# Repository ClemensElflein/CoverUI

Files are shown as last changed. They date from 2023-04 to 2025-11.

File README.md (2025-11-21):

# CoverUI for [OpenMower](https://github.com/ClemensElflein/OpenMower)

 

## About

This repository contains the firmware files required to use the mowers CoverUI (ButtonBoard).

## Variants

1. Custom DIY CoverUI-PCB which replaces the stock (top-cover) PCB.<br>
 Please check the [Cover UI board assembly instructions](<https://openmower.de/docs/cover-ui-assembly/>) for more detailed infos.<br>
 Also available in [Vermut's Shop](https://shop.devops.care/10-openmower) (as part of his 'Upgrade Kit')
1. Stock YardForce CoverUI for the following models:
   1. Classic 500 (STM32 & GD32 MCU)
   2. Classic 500B (STM32 & GD32 MCU)
   3. SA/SC/NX-Type (10 Buttons, 12 LEDs), PCB labeled with RM-ECOW-V1.0.0 (STM32 MCU)
   4. SA/SC/NX-Type (9 Buttons, 11 LEDs), PCB labeled with RM-ECOW-V1.1.0 (STM32 & GD32 MCU)
   5. NX100i (18 Buttons, 3 LEDs, 256*64 Pixel LC-Display), PCB labeled with RM-EC3-V1.1 (STM32 MCU)
   6. SAxPro (Rev6) 6 Buttons 240*128 Pixel LC-Display (STM32 MCU)
   
    For this, you need to solder some cables and flash a modified firmware to it.<br>
    Please check the detailed [Stock CoverUI Readme](Firmware/CoverUI/YardForce/README.md) (as you've also the option to use your stock 'hall', 'stop' and 'rain' cables).

## License

Distributed under the MIT License. See [LICENSE](LICENSE) for more information.

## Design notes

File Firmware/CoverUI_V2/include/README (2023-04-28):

pgmspace.h is taken from https://github.com/arduino/ArduinoCore-sam/blob/master/cores/arduino/avr/pgmspace.h
and is included as workaround for Pico

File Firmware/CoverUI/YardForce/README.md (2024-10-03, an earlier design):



[][contributors-url]
[][forks-url]
[][stars-url]
[][issues-url]
[][license-url]

<!-- CoverUI model images -->
<br />
<div align="center">
  <a href="#hardware-modifications-by-model">
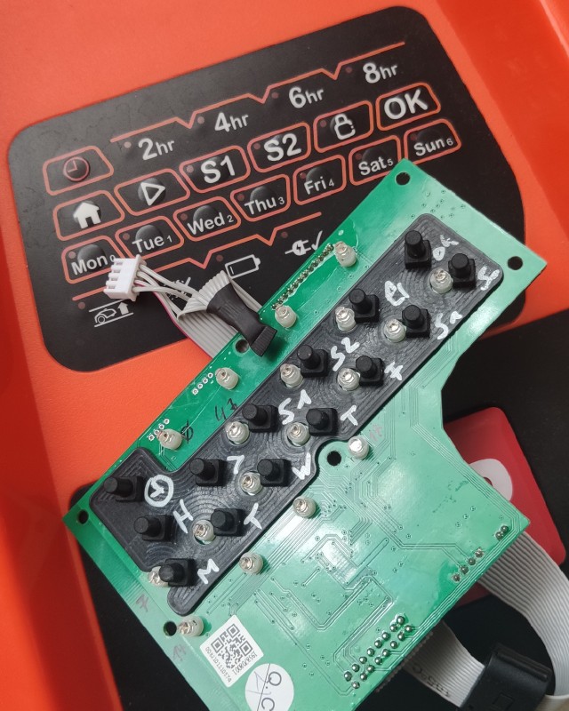
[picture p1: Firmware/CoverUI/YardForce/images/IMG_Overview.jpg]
Classic 500(B)
    
  </a>
  <a href="README-MOD-YF-SASCNX_RM-ECOW-V1.0.0.md">
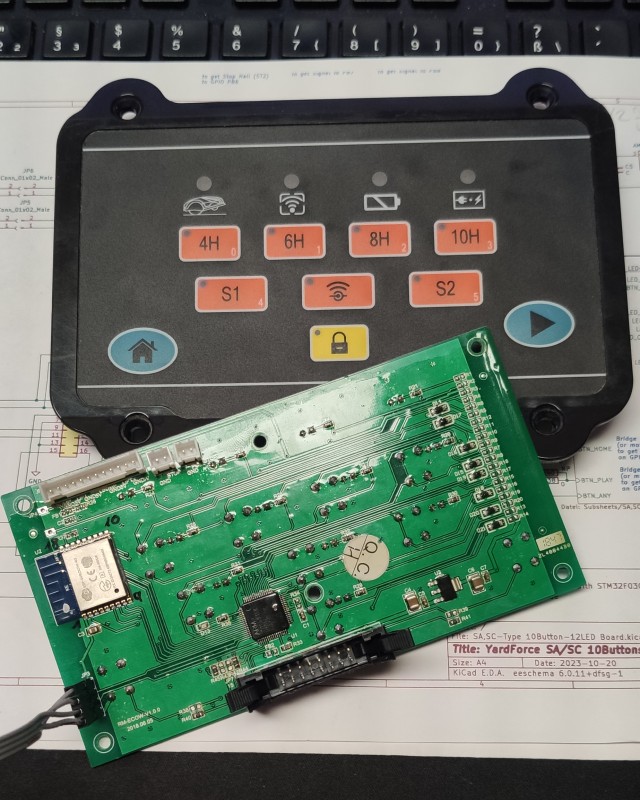
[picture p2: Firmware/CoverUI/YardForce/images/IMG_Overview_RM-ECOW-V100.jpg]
NX80i (10 Buttons, 12 LEDs) SA/SC/NX-Type CoverUI
    
  </a>
  <a href="README-MOD-YF-SASCNX_RM-ECOW-V1.1.0.md">
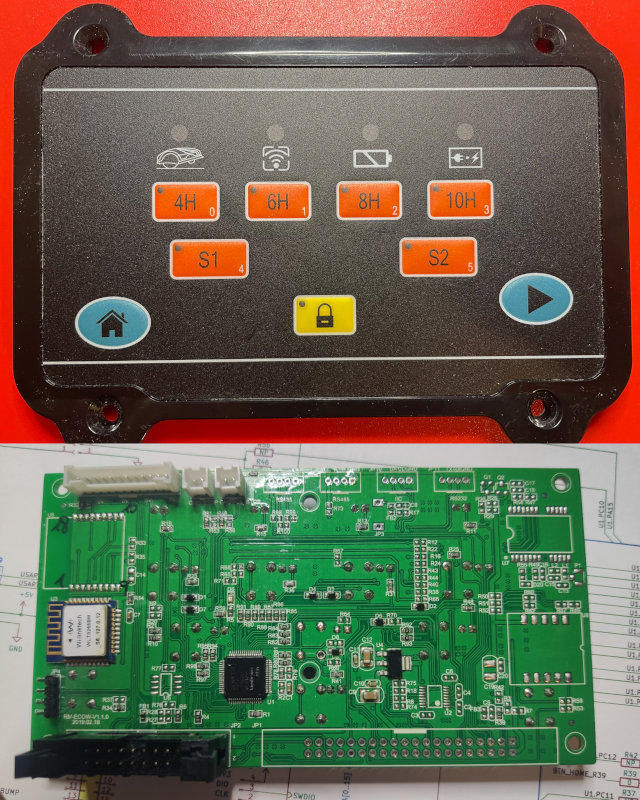
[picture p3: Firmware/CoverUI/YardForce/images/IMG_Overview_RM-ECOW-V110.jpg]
SA650 (9 Buttons, 11 LEDs) SA/SC/NX-Type CoverUI
    
  </a>
  <a href="README-MOD-YF-SASCNX_RM-EC3-V1.1.md">
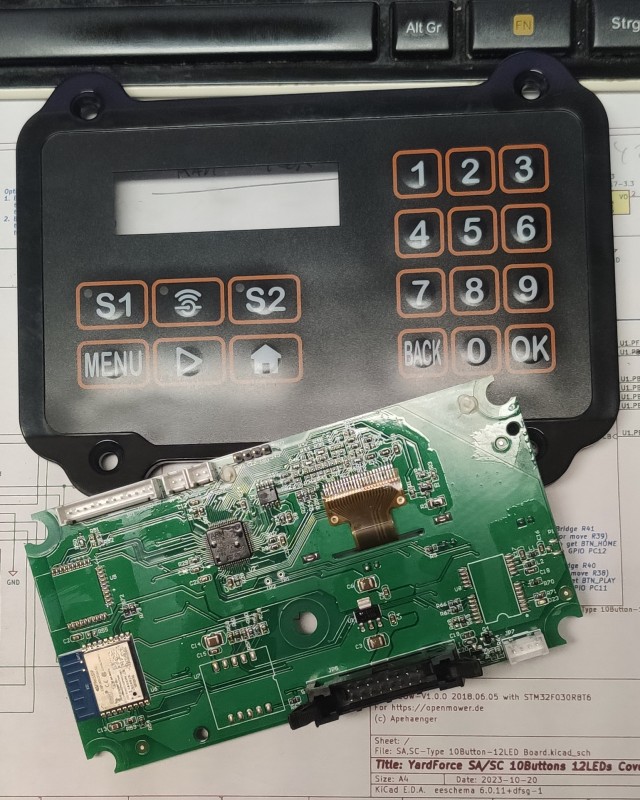
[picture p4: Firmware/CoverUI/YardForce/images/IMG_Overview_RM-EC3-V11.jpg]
NX100i (18 Buttons, 3 LEDs, 256*64 Pixel LC-Display) SA/SC/NX-Type CoverUI
    
  </a>
  <a href="README-MOD-YF-SASC_PRO_HS49067.md">
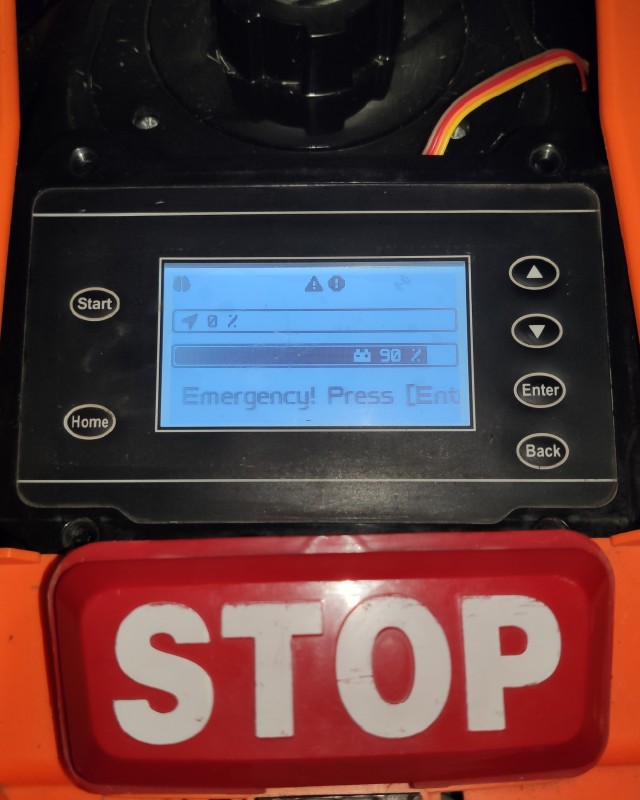
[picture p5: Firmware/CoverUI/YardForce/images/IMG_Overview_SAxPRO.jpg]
SA/SC-PRO-Type (6 Buttons, 240*160 Pixel LC-Display)
    
  </a>

  <h3 align="center">OM CoverUI Firmware for Stock YardForce PCBs</h3>

  <p align="center">

#### Tested/working with

| YardForce Model | PCB Label | <a href="https://en.wikipedia.org/wiki/Microcontroller">MCU</a> Variant |
| :--- | :---: | :---: |
| Classic 500 | RM-ECOW-V1.3.0, 2020.05.08 | STM32F030R8, GD32F330R8 |
| Classic 500B | RM-ECOW-V1.3.1, 2021.08.09 | STM32F030R8[^1], GD32F330R8 |
| SA/SC/NX-Type (10 Buttons, 12 LEDs) | RM-ECOW-V1.0.0, 2018.06.05 | STM32F030R8 |
| SA/SC/NX-Type (9 Buttons, 11 LEDs)e | RM-ECOW-V1.1.0, 2019.02.18 | STM32F030R8, GD32F330R8 |
| NX100i (18 Buttons, 3 LEDs, 256*64 Pixel LC-Display), SA/SC/NX-Type | RM-EC3-V1.1, 20210619 | STM32F401RC |
| SA/SC-PRO-Type Rev6 (6 Buttons, 240*128 Pixel LC-Display) | HS49067, WYPCB319B | STM32F030RC |

  [^1]: Not yet tested, but it's expected that it will also work flawless

  </p>
</div>

## About The Project

For those, who still have their stock *YardForce (Rev6)* Cover-UI available and want to get it running together with [OpenMower](https://github.com/ClemensElflein/OpenMower), I ported OM's CoverUI <abbr title="Firmware">FW</abbr> functionality to a couple of them (see [Tested/working with](#testedworking-with)).

<p align="right">(<a href="#readme-top">back to top</a>)</p>

## Getting Started

### Prerequisites

* Compatible stock *YardForce* Cover-UI/Button-Board or Display (see [Tested/working with](#testedworking-with))
* Soldering Iron
* ST-Link programmer/debugger

### Hardware Modifications by Model

Every CoverUI model require some hardware modifications.

Please check here, what modifications are required for your CoverUI model:

- [YardForce Classic 500, RM-ECOW-V1.3.0](README-MOD-YF-C500_RM-ECOW-V1.3.0.md)
- [YardForce Classic 500**B**, RM-ECOW-V1.3.1](README-MOD-YF-C500B_RM-ECOW-V1.3.1.md)
- [YardForce SA/SC/NX-Type 10 Buttons, 12 LEDs, RM-ECOW-V1.0.0](README-MOD-YF-SASCNX_RM-ECOW-V1.0.0.md)
- [YardForce SA/SC/NX-Type 9 Buttons, 11 LEDs, RM-ECOW-V1.1.0](README-MOD-YF-SASCNX_RM-ECOW-V1.1.0.md)
- [YardForce NX100i (SA/SC/NX-Type) 18 Buttons, 3 LEDs, 256*64 Pixel LC-Display, RM-EC3-V1.1](README-MOD-YF-SASCNX_RM-EC3-V1.1.md)
- [YardForce SA/SC-PRO-Type 6 Buttons, 240*160 Dot-Matrix-Display, HS49067](README-MOD-YF-SASC_PRO_HS49067.md)

## Flash Firmware

### Programmer/Debugger

You need an ST-Link programmer/debugger like this cheap *ST-Link (V2) clone*:

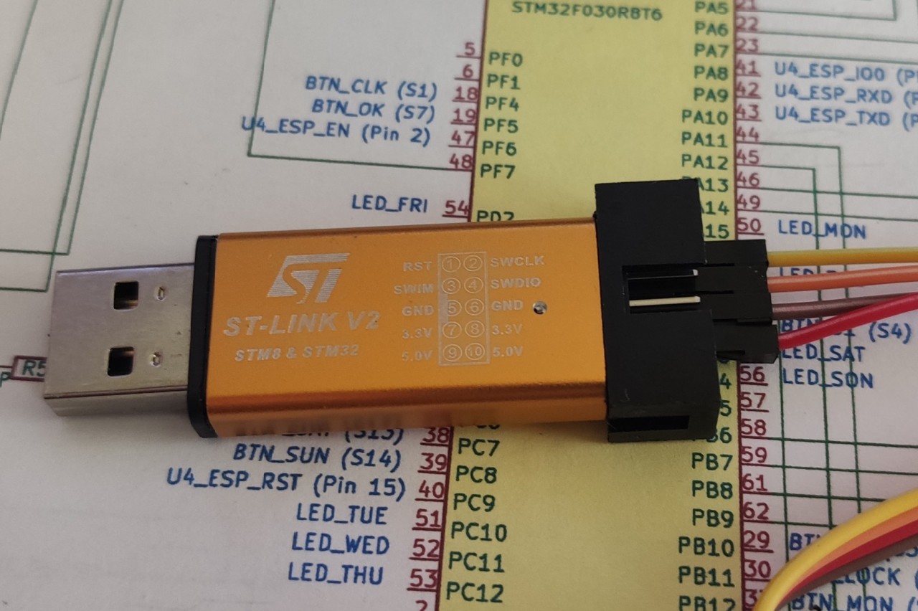
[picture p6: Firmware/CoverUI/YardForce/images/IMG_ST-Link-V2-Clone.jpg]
My ST-Link (V2) clone


There're two generic ways to get the Firmware into your MCU.<br>
Either you flash the binary directly, or you compile it by yourself with [PlatformIO](https://platformio.org/).

### Firmware binaries

1. Goto [Releases](/releases)
2. Download `firmware-stock.zip`
3. Unpack it somewhere

The file name syntax of the included firmware binaries is:  `firmware_<MDL>_<MCU>[_<opt MOD>, ...].bin`

> **Warning**
> Only install the \<MOD> version, for which you also made the required hardware modifications!
> See [Hardware Modifications by Model](#hardware-modifications-by-model)

### ST-Link (flash binary)

> **Note**
> Updated 05/07/2023

It turns out that ST-Link GUI tool is some how flawy, why I recommend to use the `st-flash` console command.

Open a terminal/console, then:

* `st-info --descr` should return either:
  * `F0xx`, which identify your PCB's MCU as a 'STM32F030R8' (i.e. Classic 500)
  * `F1xx Medium-density` or `STM32F1xx_MD` which identify a 'GD32F330R8' MCU (i.e. Classic 500)
  * `F09X` identifies a 'STM32F030RC' MCU (i.e. SAxPRO Display)
* Unplug everything from you stock CoverUI PCB and connect your ST-Link to GND, CLK, DIO and 3V3. Take special attention to hit the '3.3V' pin of your ST-Link!! Now simply:<br>
 `st-flash write firmware_<mdl>_<mcu type>[_<opt mod>, ...].bin 0x08000000` which should log at the end something like 'Flash written and verified! jolly good!'

When done, re-plug your ST-Link and you should see a quick power-on animation.

If st-flash fails with an error like "Flash memory is write protected", we need to unlock it.<br>
I used [OpenOCD][OpenOCD-url] for unlocking it. Try `openocd --version` to check if [OpenOCD][OpenOCD-url] is already installed.

Unlock your flash via:

```openocd -f interface/stlink.cfg -f target/stm32f0x.cfg -c "init" -c "halt" -c "stm32f0x unlock 0" -c "shutdown"```

Now, try again flashing by: `st-flash write firmware_<mdl>_<mcu type>[_<opt mod>, ...].bin 0x08000000`

### PlatformIO

[PlatformIO](https://platformio.org/) is a [Visual Studio Code](https://code.visualstudio.com/) extension. Once installed, do:

- `PlatformIO` (left bar)
- `PIO Home` -> `Open`
- `Open Project` cloned repository branch -> CoverUI/Firmware/CoverUI (contains platformio.ini)
- Wait till tools got loaded (bottom right status info)
- In bottombar click `Switch PlatformIO Project Environment` and choose whatever MCU, MOD & programmer/debugger- probe you use
- Wait till tools got loaded (bottom right status info)
- Finally press `PlatformIO: Upload` (right arrow symbol) in bottombar. After it compiled, linked and uploaded, it should reboot and do a short power-on LED animation.
- If you get an "Error: stm32x device protected", simply upload a second time. Look like I placed the "unlock" command some how to late. 

<p align="right">(<a href="#readme-top">back to top</a>)</p>

<!-- USAGE EXAMPLES -->
## Usage

> **Note**
> Updated 11/07/2023

Once flashed, the CoverUI should show you a quick LED animation when powered on.

### Meaning of the LEDs:

| C500(B) | SA/SC/NX-Type,<br>9&nbsp;Buttons, 11&nbsp;LEDs | SA/SC/NX-Type,<br>10&nbsp;Buttons, 12&nbsp;LEDs | NX100i<br>(SA/SC/NX-Type),<br>18&nbsp;Buttons, 3&nbsp;LEDs,<br> 256*64 Pixel LC-Display | SA/SC-PRO<br>(240*160 Pixel LC-Display) | Remark |
| :-------: | :-----: | :-------: | :----: | :----: | ----- |
| 2hr&nbsp;-&nbsp;8hr | 4H&nbsp;-&nbsp;10H | 4H&nbsp;-&nbsp;10H | <img src="images/lcd.svg" width=15% height=15%> | <img src="images/lcd.svg" width=15% height=15%> | 4 digi GPS quality progressbar. Blink = No GPS-Fix
| S1 | :heavy_check_mark: | :heavy_check_mark: | <img src="images/brain-solid.svg" width=15% height=15%> | <img src="images/brain-solid.svg" width=15% height=15%> | ROS State:<br><b>On</b> = Running (idle)<br> <b>Blink-slow</b> = Autonomous mode (mowing, (un-)docking)<br><b>Blink-fast</b> = Area recording<br><b>Off</b> = ROS not running |
| S2 | :heavy_check_mark: | :heavy_check_mark: | <img src="images/lcd.svg" width=15% height=15%> | <img src="images/lcd.svg" width=15% height=15%> | ROS Sub-State:<br><b>On</b> = not used<br> <b>Blink-slow</b> = Docking or Record-Outline<br><b>Blink-fast</b> = Undocking or Record-Obstacle<br><b>Off</b> = Idle or Mowing |
| Lifted | :heavy_check_mark: | :heavy_check_mark: | <img src="images/car-burst-solid.svg" width=15% height=15%> | <img src="images/car-burst-solid.svg" width=15% height=15%> | Emergency:<br><b>On</b> = No heart beat for more than 0.5s?!?<br> <b>Blink-slow</b> = Lifted or tilted<br><b>Blink-fast</b> = Stop button pressed<br><b>Off</b> = No Emergency |
| Wire | WLAN | WLAN | <img src="images/satellite-dish-solid.svg" width=15% height=15%> | <img src="images/satellite-dish-solid.svg" width=15% height=15%> | GPS Quality:<br><b>On</b> = \<25%<br><b>Blink-fast</b> = \<50%<br><b>Blink-slow</b> = \<75%<br><b>Off</b> = \>75% |
| Battery | :heavy_check_mark: | :heavy_check_mark: | <img src="images/car-battery-solid.svg" width=15% height=15%> | <img src="images/car-battery-solid.svg" width=15% height=15%> | <b>On</b> = Empty |
| Charge | :heavy_check_mark: | :heavy_check_mark: | <img src="images/charging-station-solid.svg" width=15% height=15%> | <img src="images/charging-station-solid.svg" width=15% height=15%> | <b>On</b> = Fully charged<br><b>Blink-slow</b> = Approx. 50% charged<br><b>Blink-fast</b> = Empty<br><b>Off</b> = Not docked |
| Mon-Sun | :x: | :x: | <img src="images/lcd.svg" width=15% height=15%> | <img src="images/lcd.svg" width=15% height=15%> | 7 digit battery-charge-state progress bar |

### Button usage:

| C500(B) | SA/SC/NX-Type,<br>9&nbsp;Buttons, 11&nbsp;LEDs | SA/SC/NX-Type,<br>10&nbsp;Buttons, 12&nbsp;LEDs | NX100i (SA/SC/NX-Type),<br>18&nbsp;Buttons, 3&nbsp;LEDs,<br> 256*64 Pixel LC-Display | SA/SC-PRO<br>(240*160 Pixel LC-Display) | Remark |
| :-------: | :----: | :---------------------------------: | :-----: | :----: | ----- |
| <kbd>Home</kbd> | :heavy_check_mark: | :heavy_check_mark: | :heavy_check_mark: | :heavy_check_mark: | Go home (docking station) |
| <kbd>▶</kbd> | :heavy_check_mark: | :heavy_check_mark: | :heavy_check_mark: | <kbd>Start</kbd> | Start mowing or continue |
| <kbd>S1</kbd> | :heavy_check_mark: | :heavy_check_mark: | :heavy_check_mark: | :x: | Start area recording if 'idle'. Pause if 'mowing' |
| <kbd>S2</kbd> | :heavy_check_mark: | :heavy_check_mark: | :heavy_check_mark: | :x: | Skip over to next area if 'mowing'. Long press (2-3s) in 'idle', delete all recorded areas! |
| <kbd>Lock</kbd> | :heavy_check_mark: | :heavy_check_mark: | :x: | <kbd>Enter</kbd> | Long press (2-3s) reset emergency |
| <kbd>OK</kbd>+<kbd>Sun</kbd> | <kbd>Lock</kbd>+<kbd>10H</kbd> | <kbd>Setup</kbd>+<kbd>10H</kbd> | <kbd>MENU</kbd>+<kbd>BACK</kbd> | :x: | Trigger power-on animation.<br>This is mainly for mounting validation, to ensure that you hit all LED guidance holes |
| <kbd>OK</kbd>+<kbd>Clock</kbd> | <kbd>Lock</kbd>+<kbd>4H</kbd> | <kbd>Setup</kbd>+<kbd>4H</kbd> | <kbd>MENU</kbd>+<kbd>0</kbd> | :x: | Display CoverUI- firmware version. LED only models will show the version as a number sequence[^2], which should show (as of writing) 206 |
| <kbd>Mon</kbd> | <kbd>4H</kbd> | <kbd>4H</kbd> | <kbd>1</kbd> | <img src="images/circle-up-solid.svg" width=20% height=20%> | Volume up[^3] |
| <kbd>Tue</kbd> | <kbd>6H</kbd> | <kbd>6H</kbd> | <kbd>2</kbd> | <img src="images/circle-down-solid.svg" width=20% height=20%> | Volume down[^3] |
| <kbd>Wed</kbd> | :x: | <kbd>8H</kbd> | <kbd>3</kbd> | <kbd>Back</kbd> | ~~Next language~~ Language selection has moved to mower_config[^3] |

[^2]: A 'number sequence' get displayed via the 'Mon(0)' to 'Sun(6)' or '4H(0)' to 'S2(5)' LEDs, whereas every short blinking 'Lifted' LED indicate a new digit.
Larger digits, get displayed with multiple digit LEDs.
I.e. 9 = 'Sun(6)' together with 'Thu(3)'

[^3]: 'Improve-Sound' branch  of 'OpenMower' Pico Firmware presupposed

<p align="right">(<a href="#readme-top">back to top</a>)</p>

## Final work

Lastly, for connecting you CoverUI, you need a cable to plug it into OM's Mainboard "UI Board" connector.

I simply cropped the 16 pin connector from my original cable and crimped OM's plug.

<span style="color:red;">But before blindly doing it, validate if the cables pin 1 mark, also matches the 16 pin female/male connector!</span>

![Cable](images/IMG_Cable.jpg)

You're done!

Plug it into `UI Board` connector of your OM mainboard and
check section [usage](#usage) about the [LED](#meaning-of-the-leds) and [Button](#button-usage) usage.

## Version History

| Version [^4] | Changes | Date |
| ------- | ------- | ---- |
| 2.06    | - Add MOD_HALL support to YardForce RM-ECOW-V1.0.0<br>- Fix heap overflow which could happen when an action button got pressed multiple (10-20) times | 2024-09-29
| 2.05    | - YardForce RM-ECOW-V1.1.0 support<br>- Backside alive LED is now software driven (hwtimer independent)<br>- Fix emergency-clear LED-countdown for RM-ECOW-V1.0.0| 2024-06-30
| 2.04    | - YardForce RM-ECOW-V1.0.0 support<br>- Dropped separate versioning<br>- Fully refactored | 2023-11-14
| 1.00    | - YardForce SAxPRO (Rev6) Dot-Matrix-Display support | 2023-09-27
| 1.00    | - Stock-Cable support for rain & hall sensors<br>- Classic 500B support | 2023-05-13
|  NA       | First OM's CoverUI port for YardForce Classic 500 | 2023-05-01

[^4]: Press sys-req button combo 'Display CoverUI- firmware version' (see [Button Usage](#button-usage)) to get your installed FW version displayed

<!-- CONTRIBUTING -->
## Contributing

Contributions are what make the open source community such an amazing place to learn, inspire, and create. Any contributions you make are **greatly appreciated**.

If you have a suggestion that would make this better, please fork the repo and create a pull request. You can also simply open an issue with the tag "enhancement".
Don't forget to give the project a star! Thanks again!

1. Fork the Project
2. Create your Feature Branch (`git checkout -b feature/AmazingFeature`)
3. Commit your Changes (`git commit -m 'Add some AmazingFeature'`)
4. Push to the Branch (`git push origin feature/AmazingFeature`)
5. Open a Pull Request

<p align="right">(<a href="#readme-top">back to top</a>)</p>

<!-- LICENSE -->
## License

Distributed under the MIT License. See `LICENSE.txt` for more information.

<p align="right">(<a href="#readme-top">back to top</a>)</p>

<!-- ACKNOWLEDGMENTS -->
## Acknowledgments

* [OpenMower](https://github.com/ClemensElflein/OpenMower)
* [Mowgli](https://github.com/cloudn1ne/Mowgli)
* [PlatformIO](https://platformio.org/)

<p align="right">(<a href="#readme-top">back to top</a>)</p>

<!-- MARKDOWN LINKS & IMAGES -->
<!-- https://www.markdownguide.org/basic-syntax/#reference-style-links -->
[contributors-shield]: https://img.shields.io/github/contributors/ClemensElflein/CoverUI.svg?style=for-the-badge
[contributors-url]: https://github.com/ClemensElflein/CoverUI/graphs/contributors
[forks-shield]: https://img.shields.io/github/forks/ClemensElflein/CoverUI.svg?style=for-the-badge
[forks-url]: https://github.com/ClemensElflein/CoverUI/network/members
[stars-shield]: https://img.shields.io/github/stars/ClemensElflein/CoverUI.svg?style=for-the-badge
[stars-url]: https://github.com/ClemensElflein/CoverUI/stargazers
[issues-shield]: https://img.shields.io/github/issues/ClemensElflein/CoverUI.svg?style=for-the-badge
[issues-url]: https://github.com/ClemensElflein/CoverUI/issues
[license-shield]: https://img.shields.io/github/license/ClemensElflein/CoverUI.svg?style=for-the-badge
[license-url]: https://github.com/ClemensElflein/CoverUI/blob/master/LICENSE.txt
[OpenOCD-url]: https://openocd.org/pages/about.html

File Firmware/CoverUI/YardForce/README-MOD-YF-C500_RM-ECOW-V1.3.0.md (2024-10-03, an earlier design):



([back to README][README])

## YardForce Classic 500, RM-ECOW-V1.3.0 MODs

Classic 500

### Buttons (*mandatory*)

With the stock component placement, Button-Home and Button-Play get routed to the main (black) 16 pin connector (JP2/J6).
But we need them routed to the MCU.
Luckily the PCB is already prepared for this.

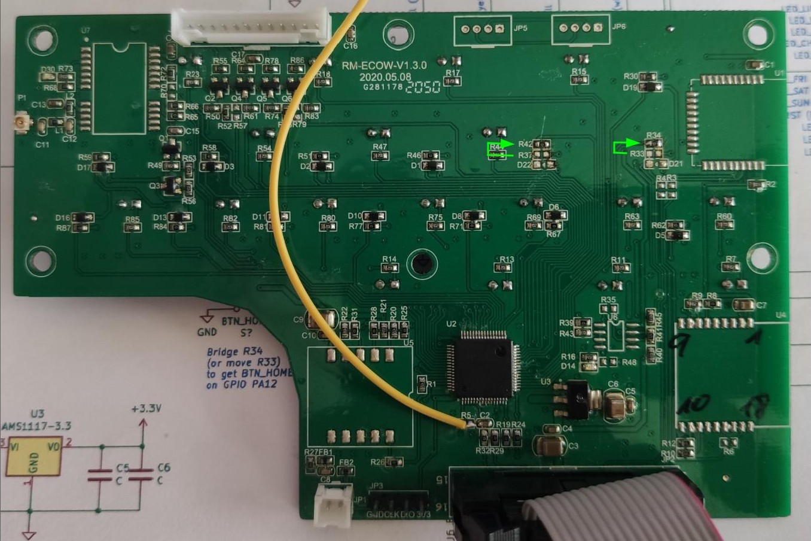
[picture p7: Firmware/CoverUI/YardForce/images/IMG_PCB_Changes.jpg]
Mandatory Hardware Modification Open in browser

<sup>(The yellow cable (to R5/C2) should not harm you. This is the NRST signal which is only required if you bug the code (like me) during development)</sup>

Move the 0 Ohm (bridge) resistors:
1. R33 to the NonPlaced R34 position (Button-Home)
2. R37 to (NP) R42 (Button-Play)
   
You might also simply bridge R34 and R42, but for me it was simpler to move them

<p align="right">(<a href="#readme-top">back to top</a>)</p>

### Rain Sensor (*optional*)

If you also like to use the Stock-Rain-Sensor cabling, you need to solder a separate cable from FB2 to the non-placed R79.
See the yellow cable on the following images:

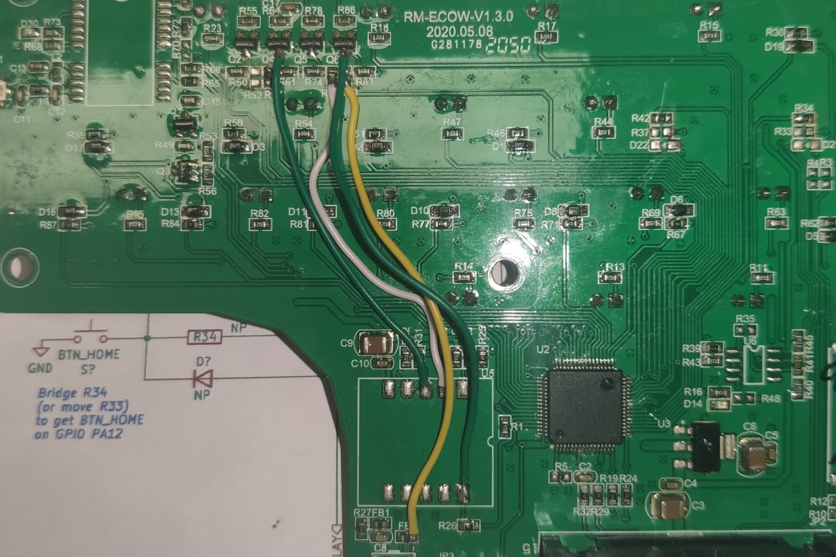
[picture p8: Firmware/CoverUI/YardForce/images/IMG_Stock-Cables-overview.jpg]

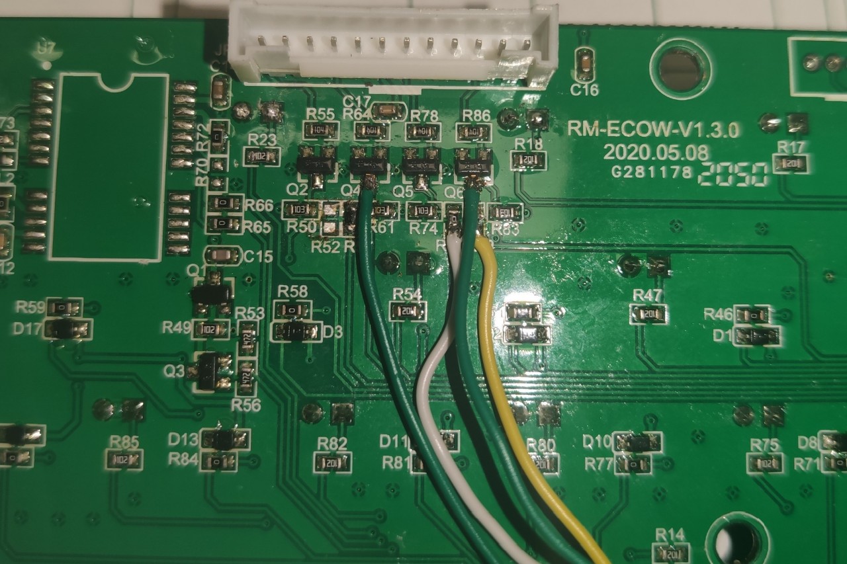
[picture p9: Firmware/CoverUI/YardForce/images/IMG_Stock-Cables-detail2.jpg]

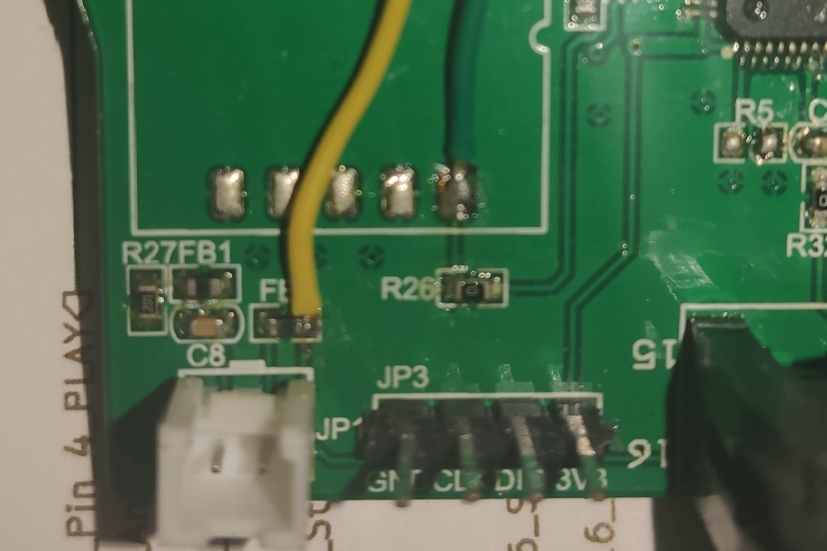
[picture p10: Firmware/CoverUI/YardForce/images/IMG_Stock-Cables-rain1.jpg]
Optional Rain Hardware Modification Open in browser


<p align="right">(<a href="#readme-top">back to top</a>)</p>

### Emergency Hall Sensors (*optional*)

If you also like to use your Stock-Hall-Sensor cabling (2 \* stop-button & 2 \* wheel-lift):
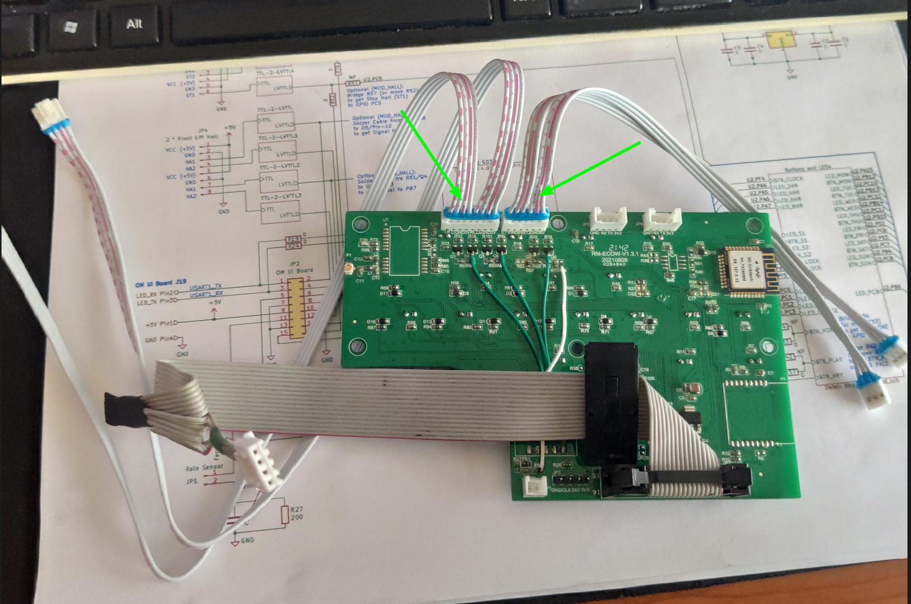
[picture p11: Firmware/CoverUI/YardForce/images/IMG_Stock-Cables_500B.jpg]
Optional Hall Cables

Then you need to solder one more R- bridge as well as 3 more separate cables.
Take into **attention** that you need to make all 4 steps:

1. Move R52 to (non-placed) R57 (see green arrow on image), or simple bridge R57 (i.e. with 32kg solder)
2. Solder a cable-bridge from Q4/R61 to U5/Pin3 (see left green cable)
3. Solder a cable-bridge from the bottom end of R76 to U5/Pin2 (see white cable)
4. Solder a cable-bridge from Q6/R83 to U5/Pin10 (see right green cable)

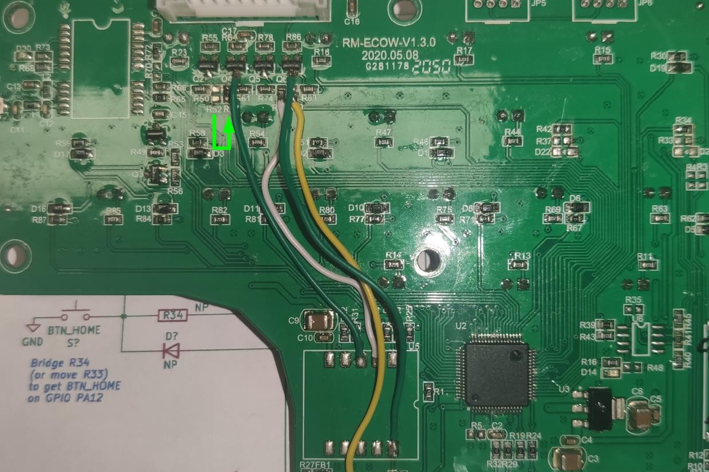
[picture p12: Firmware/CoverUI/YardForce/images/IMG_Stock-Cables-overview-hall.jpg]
Optional Hall Hardware Modification Open in browser

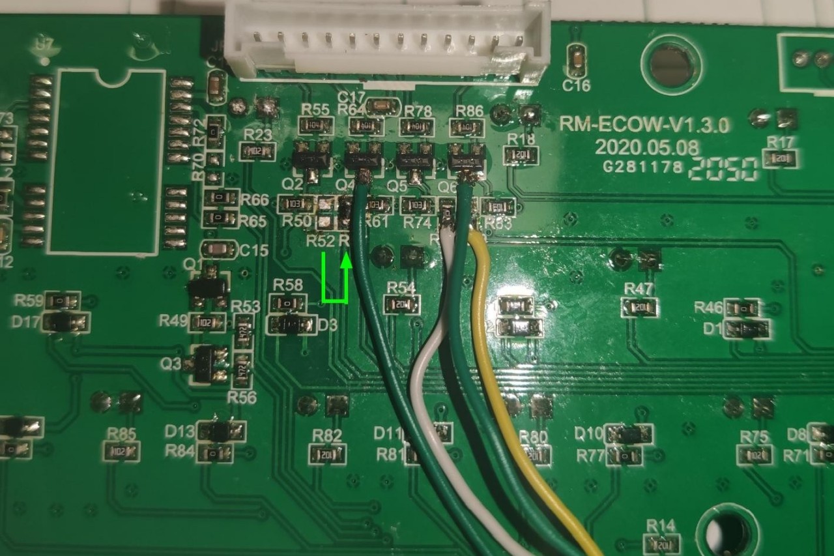
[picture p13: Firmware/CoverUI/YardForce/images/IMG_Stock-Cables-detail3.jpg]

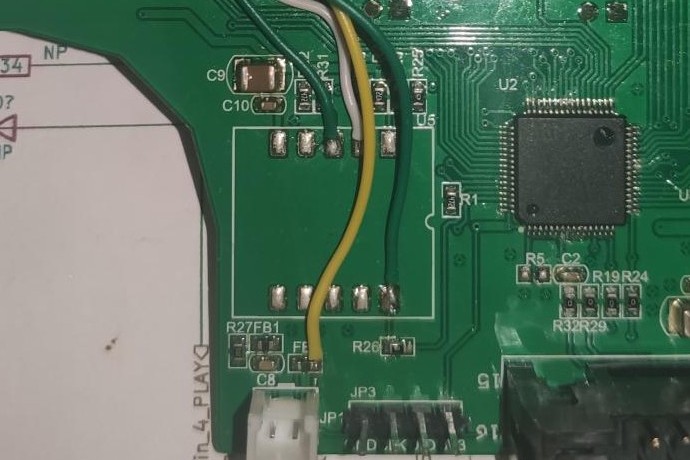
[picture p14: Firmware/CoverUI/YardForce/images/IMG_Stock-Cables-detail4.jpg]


I only made it with colored cables for a more clear documentation.
If you've repair-wire like [this](https://de.farnell.com/roadrunner/rrp-a-105/draht-0-15mm-sortiert-pk-4/dp/5017233), it might look better, like this:

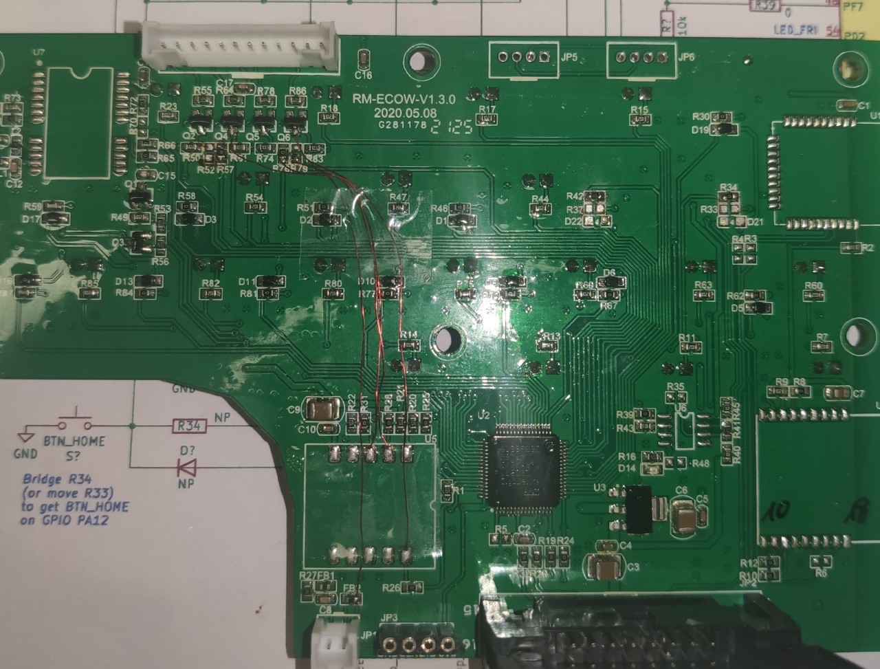
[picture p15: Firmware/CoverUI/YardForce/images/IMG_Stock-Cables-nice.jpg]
Hardware Changes Hall nice


<p align="right">(<a href="#readme-top">back to top</a>)</p>

([back to README][README])

[README]: README.md

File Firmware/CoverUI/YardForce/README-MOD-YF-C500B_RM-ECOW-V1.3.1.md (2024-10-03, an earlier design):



([back to README][README])

## YardForce Classic 500B, RM-ECOW-V1.3.1 MODs

Classic 500

### Buttons (*mandatory*)

With the stock component placement, Button-Home and Button-Play get routed to the main (black) 16 pin connector (JP2/J6).
But we need them routed to the MCU.
Luckily the PCB is already prepared for this.

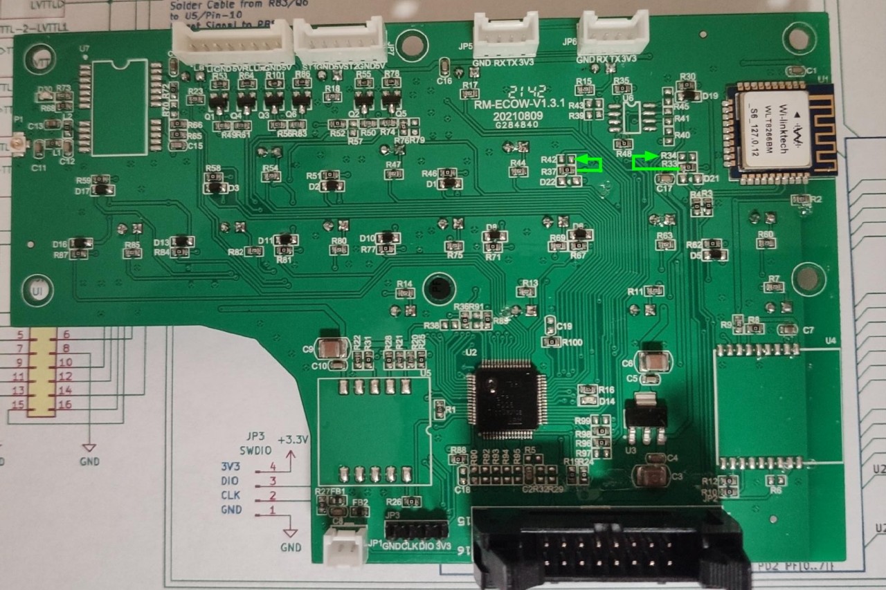
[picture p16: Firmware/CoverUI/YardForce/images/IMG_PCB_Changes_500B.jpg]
Mandatory Hardware Modification Open in browser


Move the 0 Ohm (bridge) resistors:

1. R33 to the NonPlaced R34 position (Button-Home)
2. R37 to (NP) R42 (Button-Play)

You might also simply bridge R34 and R42, but for me it was simpler to move them

<p align="right">(<a href="#readme-top">back to top</a>)</p>

### Rain Sensor (*optional*)

If you also like to use the Stock-Rain-Sensor cabling, you need to solder a separate cable from FB2 to the non-placed R79.
See the white cable on the following images:

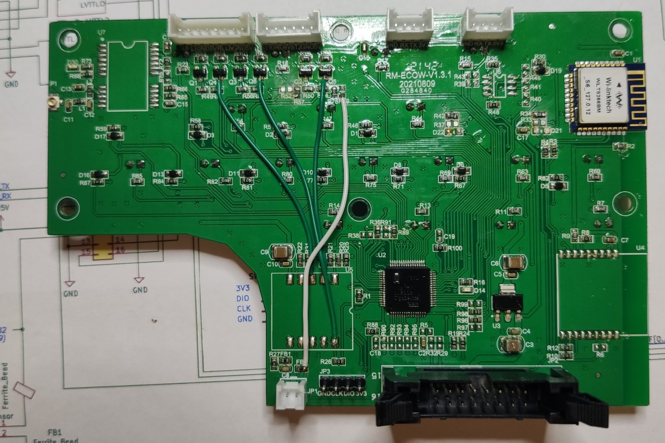
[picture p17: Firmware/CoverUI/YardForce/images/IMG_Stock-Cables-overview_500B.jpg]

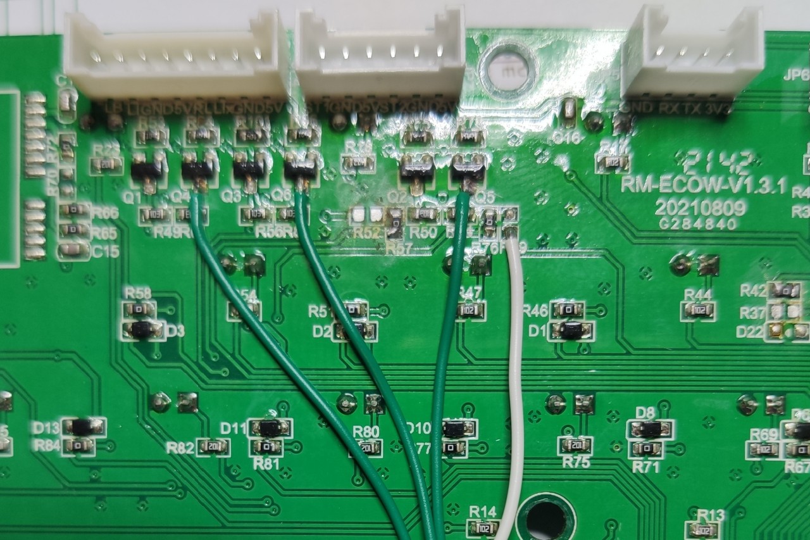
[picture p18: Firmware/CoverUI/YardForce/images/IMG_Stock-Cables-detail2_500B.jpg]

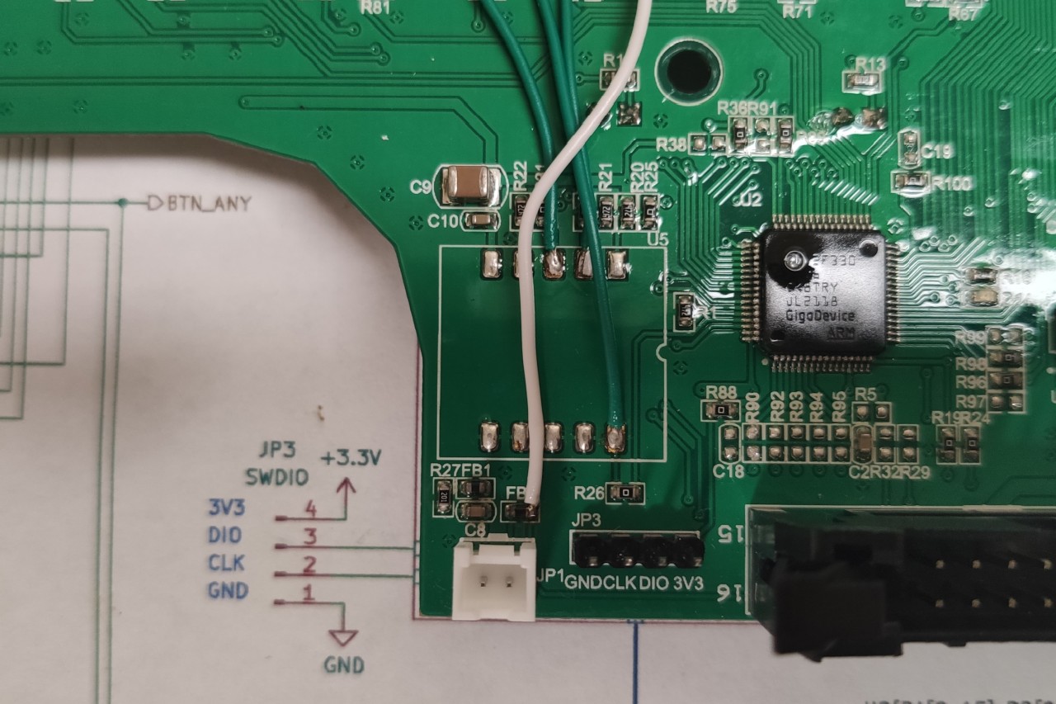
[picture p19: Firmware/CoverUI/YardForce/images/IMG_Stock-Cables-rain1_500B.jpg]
Optional Rain Hardware Modification Open in browser


<p align="right">(<a href="#readme-top">back to top</a>)</p>

### Emergency Hall Sensors (*optional*)

If you also like to use your Stock-Hall-Sensor cabling (2 \* stop-button & 2 \* wheel-lift):
Optional Hall Cables
Then you need to solder one more R- bridge as well as 3 more separate cables.
Take into **attention** that you need to make all 4 steps:

1. Move R52 to (non-placed) R57 (see green arrow on image), or simple bridge R57 (i.e. with 32kg solder)
2. Solder a cable-bridge from Q4/R61 to U5/Pin3 (see left green cable)
3. Solder a cable-bridge from the bottom end of R76 to U5/Pin2 (see middle green cable)
4. Solder a cable-bridge from Q6/R83 to U5/Pin10 (see right green cable)

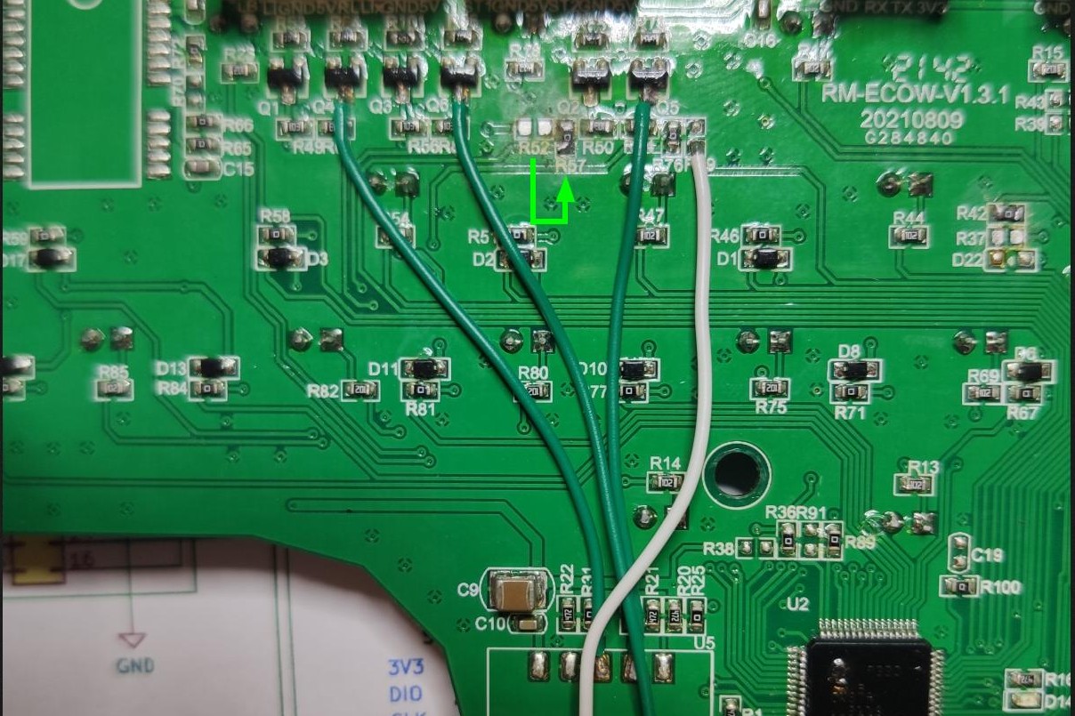
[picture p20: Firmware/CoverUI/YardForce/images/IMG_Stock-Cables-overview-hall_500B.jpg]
Optional Hall Hardware Modification Open in browser

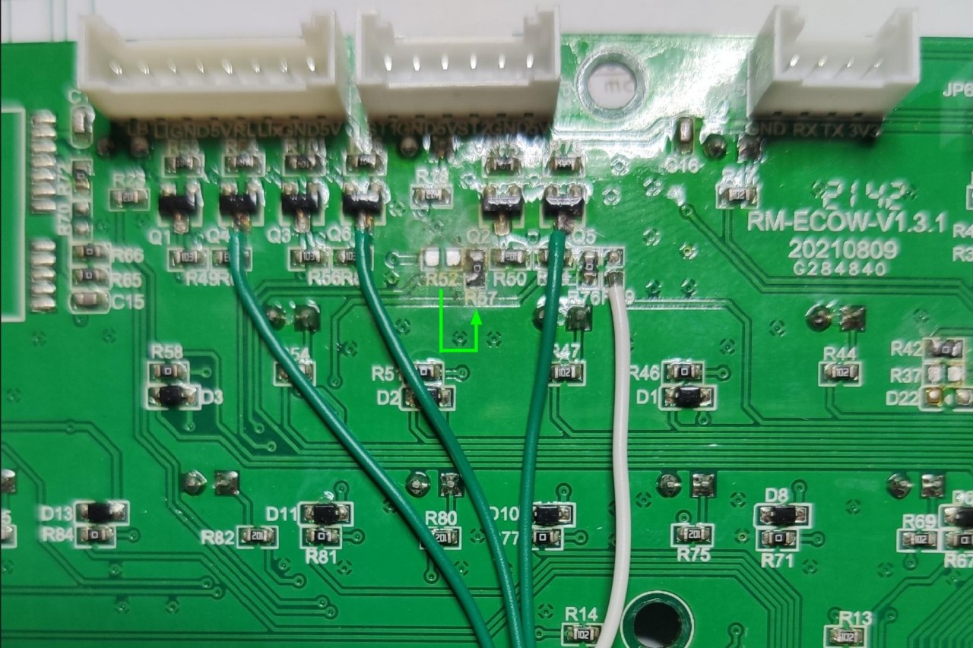
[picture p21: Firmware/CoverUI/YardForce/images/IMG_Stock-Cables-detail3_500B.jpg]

Optional Hall Hardware Modification Open in browser

I only made it with colored cables for a more clear documentation.
If you've repair-wire like [this](https://de.farnell.com/roadrunner/rrp-a-105/draht-0-15mm-sortiert-pk-4/dp/5017233), it might look better, like this:

Hardware Changes Hall nice

<p align="right">(<a href="#readme-top">back to top</a>)</p>

([back to README][README])

[README]: README.md

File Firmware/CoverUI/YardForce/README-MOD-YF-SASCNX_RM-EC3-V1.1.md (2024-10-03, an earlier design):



([back to README][README])

## YardForce SA/SC/NX-Type 18 Buttons, 3 LEDs, 256*64 Pixel LC-Display, RM-EC3-V1.1 MODs

YardForce NX100i

### Buttons (*mandatory*)

With the stock component placement, Button-Home and Button-Play get routed to the main (black) 16 pin connector (JP5).
But we need them routed to the MCU.

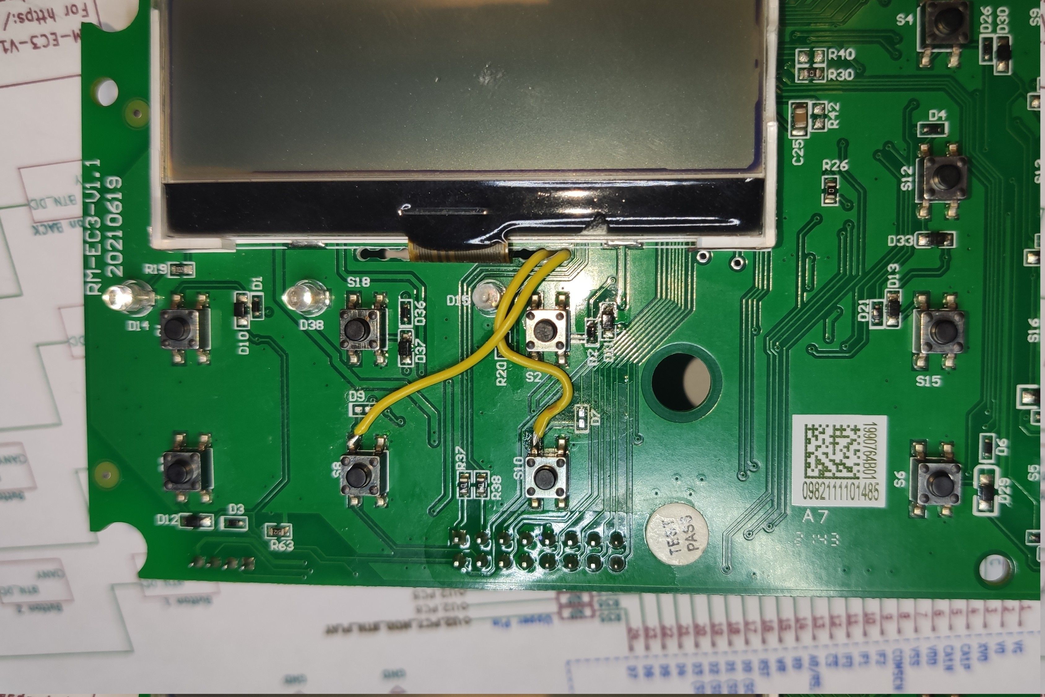
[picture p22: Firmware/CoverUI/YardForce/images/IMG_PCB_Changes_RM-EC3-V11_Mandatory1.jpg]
Mandatory Hardware Modification Open in browser

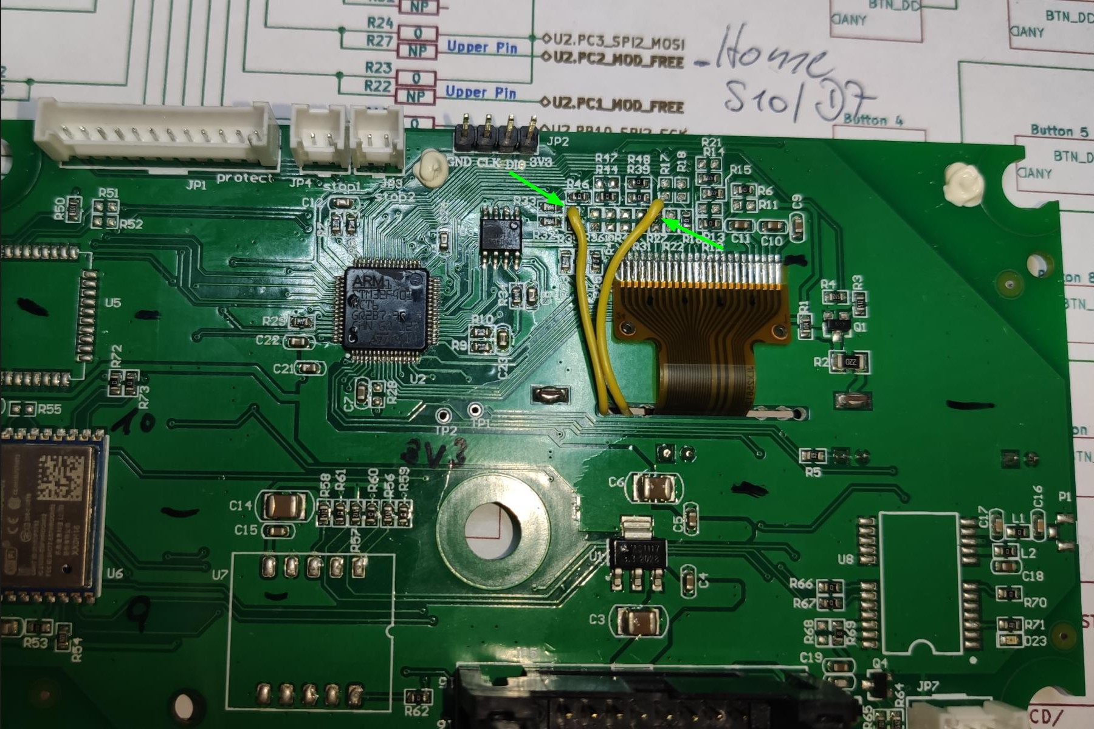
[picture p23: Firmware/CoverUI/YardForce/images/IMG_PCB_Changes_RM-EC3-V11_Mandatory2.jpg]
Mandatory Hardware Modification Open in browser


Solder two cables:

1. S8/D9 front-side, to back-side R35-upper-pin (Play button)
2. S10/D7 front-side, to back-side R27-upper-pin (Home button)

<p align="right">(<a href="#readme-top">back to top</a>)</p>

### Emergency Stop Switches (*optional*)

If you also like to use your two Stock-Stop-Switch cables, and you should, because you need the four OM- Hall-Plugs for the remaining hall-sensors:

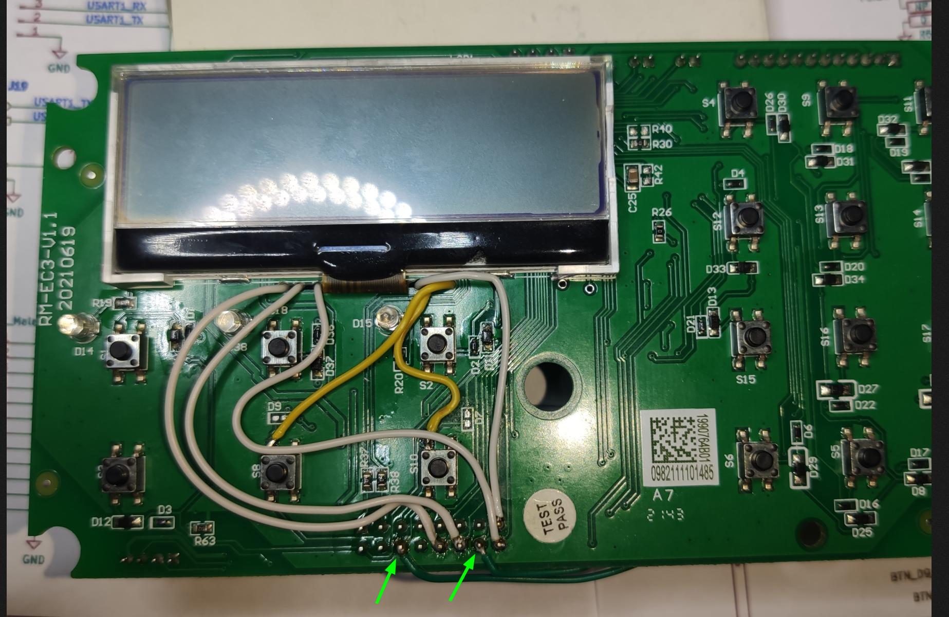
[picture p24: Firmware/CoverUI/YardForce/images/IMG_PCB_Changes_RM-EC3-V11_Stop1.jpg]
Optional Stop Hardware Modification Open in browser

Optional Stop Hardware Modification Open in browser

Solder another two cables:

1. JP5-Pin14 front-side, to back-side U7-Pin1
2. JP5-Pin6 front-side, to back-side U7-Pin2

<p align="right">(<a href="#readme-top">back to top</a>)</p>

### Emergency Hall Switches (*optional*)

If you also like to use your original "4-leg cable for the 4 hall sensors", then you need to solder 4 more cables:

Optional Stop Hardware Modification Open in browser
Optional Stop Hardware Modification Open in browser

Solder four cables:

1. JP5-Pin15 front-side, to back-side R17-lower-pin
2. JP5-Pin16 front-side, to back-side R18-upper-pin
3. JP5-Pin12 front-side, to back-side R13-right-pin
4. JP5-Pin10 front-side, to back-side R21-right-pin

> **Warning**
> As you might know, the hall sensors are driven by 5V, whereas the MCU is running at 3.3V.
> All used GPIO ports of this modification, are so called "5V tolerant" ports.
> But there might happen electrical cases like: VREG delay or short on 3.3V line, which could kill the "5V tolerant" pin of your MCU.
> To be on the save side for such odd things happen, I highly advice to remove the 5V pull-up resistor on your Hall-PCB, or move it aside like shown on this picture:

Optional Remove Hall Pull-Up Resistor Open in browser

<p align="right">(<a href="#readme-top">back to top</a>)</p>

([back to README][README])

[README]: README.md

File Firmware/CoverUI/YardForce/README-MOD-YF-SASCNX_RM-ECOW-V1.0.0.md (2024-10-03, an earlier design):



([back to README][README])

## YardForce SA/SC/NX-Type 10 Buttons, 12 LEDs, RM-ECOW-V1.0.0 MODs

  YardForce NX80i

### Buttons (*mandatory*)

With the stock component placement, Button-Home and Button-Play get routed to the main (black) 16 pin connector (JP2/J6).
But we need them routed to the MCU.
Luckily the PCB is already prepared for this.

Mandatory Hardware Modification Open in browser

Move the 0 Ohm (bridge) resistors:

1. R39 to the NonPlaced R41 position (Button-Home)
2. R38 to (NP) R40 (Button-Play)

You might also simply bridge R40 and R41, but for me it was simpler to move them

<p align="right">(<a href="#readme-top">back to top</a>)</p>

### Emergency Hall Switches (*optional*)

If you also like to use your original "4-leg cable for the 4 hall sensors", then you need to solder 4 more cables:

Optional Hall Hardware Modification Open in browser
Optional Hall Hardware Modification 2 Open in browser

Solder four cables:

1. JP2-Pin10 to U2-Pin6 (LIFTX to PF6)
2. JP2-Pin12 to U2-Pin7 (LBUMP to PA12)
3. JP2-Pin15 to U2-Pin8 (RBUMP to PA11)
4. JP2-Pin16 to U2-Pin17 (LIFT to PA8)

> **Warning**
> As you probably know, the hall sensors are driven by 5V, whereas the MCU is running at 3.3V.<br>
> All used GPIO ports of this modification, are so called "5V tolerant" ports.<br>
> **But** there might happen electrical cases like: VREG delay or short on 3.3V line, which could kill the "5V tolerant" pin of your MCU.
> To be on the save side for such odd cases, I highly recommend to remove the 5V pull-up resistor from your Hall-PCB, or move it aside like shown on this picture:

Optional Remove Hall Pull-Up Resistor Open in browser

<p align="right">(<a href="#readme-top">back to top</a>)</p>

### Emergency Stop Switches (*optional*)

If you also like to use your two Stock-Stop-Switch cables, and you should, as you need the four OM- Hall-Plugs for the remaining hall-sensors:

Optional Hall Hardware Modification Open in browser

Move the 0 Ohm (bridge) resistors:

1. R42 to the NonPlaced R44 position (JP5 Stop)
2. R43 to (NP) R45 (JP6 Stop)

You might also simply bridge R44 and R45, but for me it was simpler to move them

([back to README][README])

[README]: README.md

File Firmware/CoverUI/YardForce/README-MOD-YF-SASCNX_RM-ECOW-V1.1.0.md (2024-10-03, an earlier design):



([back to README][README])

## YardForce SA/SC/NX-Type 9 Buttons, 11 LEDs, RM-ECOW-V1.1.0 MODs

YardForce SA650

### Buttons (*mandatory*)

With the stock component placement, Button-Home and Button-Play get routed to the main (black) 16 pin connector (JP2).
But we need them routed to the MCU.
Luckily the PCB is already prepared for this.

Mandatory Hardware Modification Open in browser

Move the 0 Ohm (bridge) resistors:

1. R39 to the NonPlaced R42 position (Button-Home)
2. R34 to (NP) R37 (Button-Play)

You might also simply bridge R42 and R37, but for me it was simpler to move them.

<p align="right">(<a href="#readme-top">back to top</a>)</p>

### Emergency Hall Switches (*optional*)

If you also like to use your original "4-leg cable for the 4 hall sensors", then you need to solder 4 more cables:

Optional Hall Hardware Modification Open in browser

Solder four cables:

1. JP1-Pin39 to U6-Pin8 (RBUMP to PC9)
2. JP1-Pin40 to U6-Pin2 (LIFT to PA8)
3. JP1-Pin36 to U6-Pin15 (LBUMP to PC8)
4. JP1-Pin34 to R8-left-pin (LIFTX to PA9)

> **Warning**
> As you probably know, the hall sensors are driven by 5V, whereas the MCU is running at 3.3V.<br>
> All used GPIO ports of this modification, are so called "5V tolerant" ports.<br>
> **But** there might happen electrical cases like: VREG delay or short on 3.3V line, which could kill the "5V tolerant" pin of your MCU.
> To be on the save side for such odd cases, I highly recommend to remove the 5V pull-up resistor from your Hall-PCB, or move it aside like shown on this picture:

Optional Remove Hall Pull-Up Resistor Open in browser

<p align="right">(<a href="#readme-top">back to top</a>)</p>

### Emergency Stop Switches (*optional*)

If you also like to use your 2 stock Stop-Switch cables, you need to bridge or move 2 further resistors:

Optional Hall Hardware Modification Open in browser

Move the 0 Ohm (bridge) resistors:

1. R61 to the NonPlaced R63 position (JP8 Stop)
2. R46 to (NP) R56 (JP6 PC8-Stop)

You might also simply bridge R63 and R56, but for me it was simpler to move them.

<p align="right">(<a href="#readme-top">back to top</a>)</p>

([back to README][README])

[README]: README.md

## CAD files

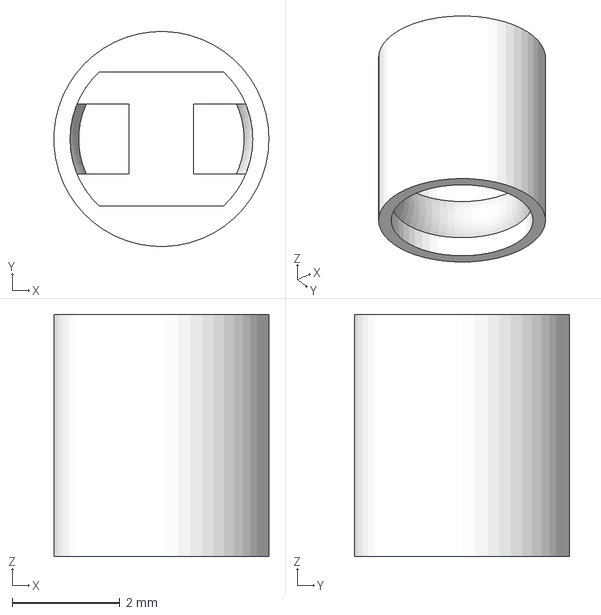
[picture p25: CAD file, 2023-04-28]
Hardware/grabcad/FIX-LEDS-4.5.step
4.00 x 4.00 x 4.50 mm

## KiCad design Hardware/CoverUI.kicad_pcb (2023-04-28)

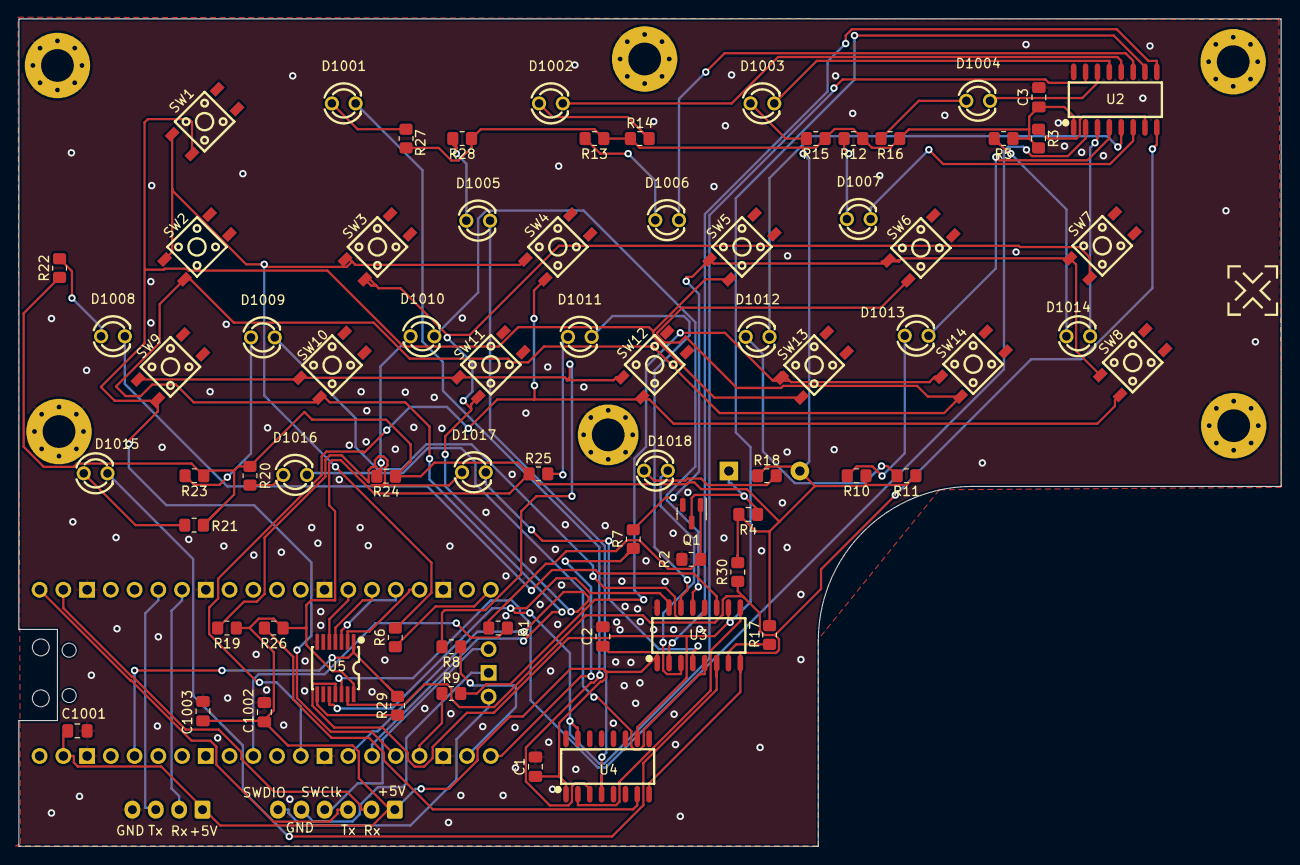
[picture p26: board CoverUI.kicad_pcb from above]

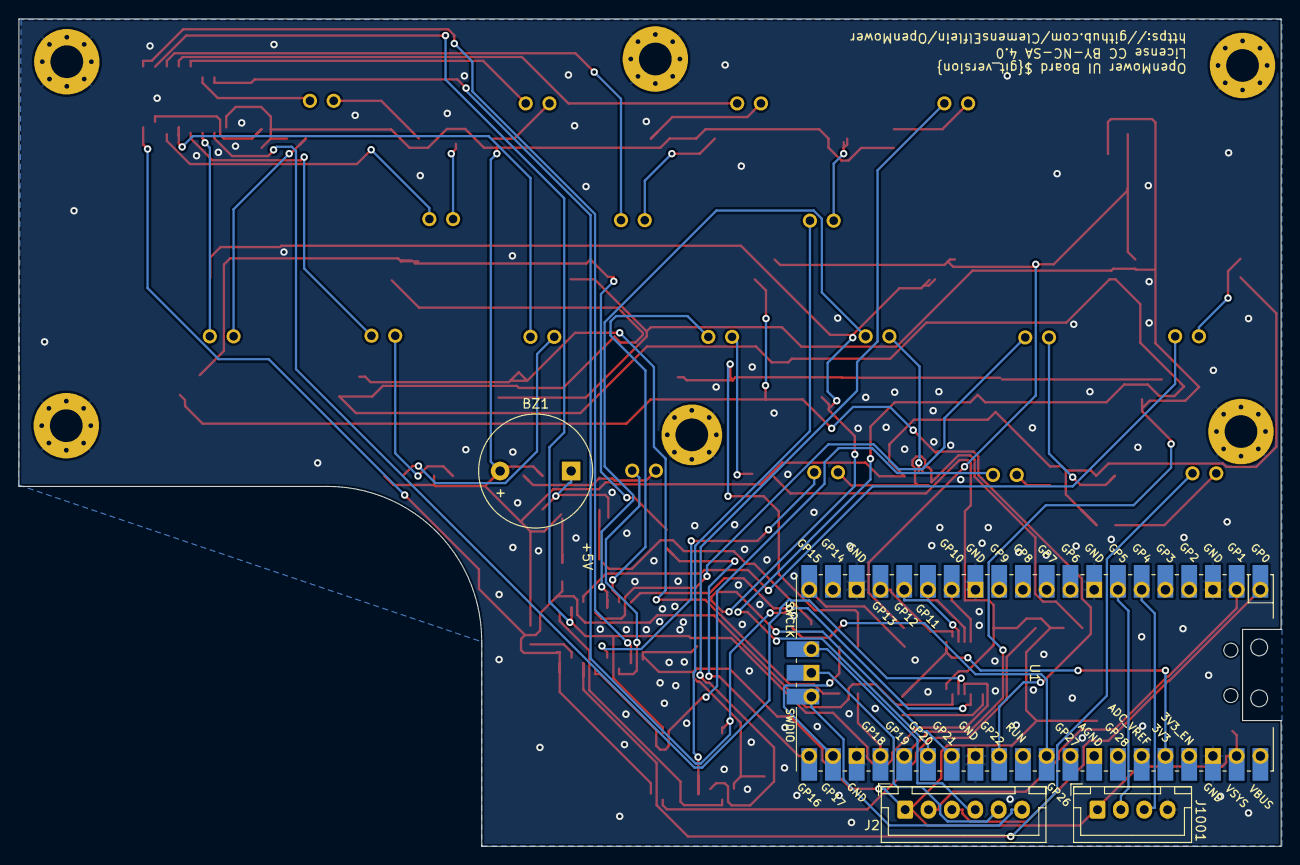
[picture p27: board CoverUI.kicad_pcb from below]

Board: 2 copper layers, 135.0 x 88.5 mm, 102 parts (4 on the bottom side), 75 nets.

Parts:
BZ1: Buzzer; Buzzer_12x9.5RM7.6
C1, C2, C3, C1001, C1002: 100nF; C_0805_2012Metric_Pad1.18x1.45mm_HandSolder
C1003: 1uF; C_0805_2012Metric_Pad1.18x1.45mm_HandSolder
D1001, D1002, D1003, D1004, D1005, D1006, D1007, D1008, D1009, D1010, D1011, D1012, D1013, D1014, D1015, D1016, D1017, D1018: 20mA 2V, Red; LED-TH_BD3.0-P2.54-FD
H1001, H1002, H1003, H1004, H1005, H1006: MountingHole_Pad; MountingHole_3.5mm_Pad_Via
J2: Conn_01x06_Male; JST_XH_B6B-XH-A_1x06_P2.50mm_Vertical
J1001: Conn_01x04_Male; JST_XH_B4B-XH-A_1x04_P2.50mm_Vertical
Q1: BSS138; SOT-23
R1, R4: 1k; R_0805_2012Metric_Pad1.20x1.40mm_HandSolder
R2: 47k; R_0805_2012Metric_Pad1.20x1.40mm_HandSolder
R3, R6, R7, R8, R9, R17, R26, R29, R30: 10k; R_0805_2012Metric_Pad1.20x1.40mm_HandSolder
R5, R10, R11, R12, R13, R14, R15, R16, R18, R19, R20, R21, R22, R23, R24, R25, R27, R28: 150; R_0805_2012Metric_Pad1.20x1.40mm_HandSolder
SP01, SP02, SP03, SP04, SP05, SP06, SP07, SP08, SP09, SP10, SP11, SP12, SP13, SP14, SP15, SP16: LedSpacer; LED_SPACER_3mm
SP17, SP18, SP20: LED_SPACER_3mm
SW1, SW2, SW3, SW4, SW5, SW6, SW7, SW8, SW9, SW10, SW11, SW12, SW13, SW14: SW_MEC_5G; SW-SMD_4P-L4.5-W4.5-P3.00-LS7.0
U1: Raspberry-Pico; RPi_Pico_SMD_TH
U2, U3, U4: TPIC6C596DRG4; SOIC-16_L10.8-W4.5-P1.27-LS6.8-BL
U5: RS0104YQ; TSSOP-14_L5.0-W4.4-P0.65-LS6.4-BL

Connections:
+3.3V: R29.2, U1.36 (3V3), U5.1 (VCCA)
+5V: BZ1.2 (+), C1.1, C2.1, C3.1, C1001.1, C1002.1, C1003.1, J2.1, J1001.1, R3.1, R4.2, R5.1, R10.1, R11.1, R12.1, R13.1, R14.1, R15.1, R16.1, R17.1, R18.1, R19.1, R20.1, R21.1, R22.1, R23.1, R24.1, R25.1, R26.1, R27.1, R28.1, R30.2, U1.39 (VSYS), U2.1 (VCC), U3.1 (VCC), U4.1 (VCC), U5.14 (VCCB)
/LEDmux/G: R30.1, U2.8 (~G), U3.8 (~G), U4.8 (~G), U5.13 (B1)
/LEDmux/G_3.3V: U1.17 (GPIO13), U5.2 (A1)
/LEDmux/RCK: U2.10 (RCK), U3.10 (RCK), U4.10 (RCK), U5.11 (B3)
/LEDmux/RCK_3.3V: U1.15 (GPIO11), U5.4 (A3)
/LEDmux/SER: U2.2 (SER/IN), U5.12 (B2)
/LEDmux/SER_3.3V: U1.16 (GPIO12), U5.3 (A2)
/LEDmux/SRCK: U2.15 (SRCK), U3.15 (SRCK), U4.15 (SRCK), U5.10 (B4)
/LEDmux/SRCK_3.3V: U1.14 (GPIO10), U5.5 (A4)
/RaspberryPico/GP15: R6.1, U1.20 (GPIO15)
/RaspberryPico/GP16: R7.1, U1.21 (GPIO16)
/RaspberryPico/GP17: R8.1, U1.22 (GPIO17)
/RaspberryPico/GP18: R9.1, U1.24 (GPIO18)
/RaspberryPico/GP19: SW1.3 (B), SW5.3 (B), SW9.3 (B), SW13.3 (B), U1.25 (GPIO19)
/RaspberryPico/GP20: SW2.3 (B), SW6.3 (B), SW10.3 (B), SW14.3 (B), U1.26 (GPIO20)
/RaspberryPico/GP21: SW3.3 (B), SW7.3 (B), SW11.3 (B), U1.27 (GPIO21)
/RaspberryPico/GP22: SW4.3 (B), SW8.3 (B), SW12.3 (B), U1.29 (GPIO22)
/RaspberryPico/GP26: R1.1, U1.31 (GPIO26_ADC0)
/RaspberryPico/PiCo_RX: J1001.2, U1.7 (GPIO5)
/RaspberryPico/PiCo_TX: J1001.3, U1.6 (GPIO4)
GND: C1.2, C2.2, C3.2, C1001.2, C1002.2, C1003.2, H1001.1, H1002.1, H1003.1, H1004.1, H1005.1, H1006.1, J1001.4, Q1.2 (S), R2.2, U1.3 (GND), U1.8 (GND), U1.13 (GND), U1.18 (GND), U1.23 (GND), U1.28 (GND), U1.38 (GND), U2.16 (GND), U3.16 (GND), U4.16 (GND), U5.7 (GND)
unnamed: BZ1.1 (-), Q1.3 (D), R4.1
unnamed: D1001.1 (A), R27.2
unnamed: D1001.2 (K), U4.3 (DRAIN0)
unnamed: D1002.1 (A), R14.2
unnamed: D1002.2 (K), U2.12 (DRAIN5)
unnamed: D1003.1 (A), R15.2
unnamed: D1003.2 (K), U2.13 (DRAIN6)
unnamed: D1004.1 (A), R16.2
unnamed: D1004.2 (K), U2.14 (DRAIN7)
unnamed: D1005.1 (A), R28.2
unnamed: D1005.2 (K), U4.4 (DRAIN1)
unnamed: D1006.1 (A), R13.2
unnamed: D1006.2 (K), U2.11 (DRAIN4)
unnamed: D1007.1 (A), R12.2
unnamed: D1007.2 (K), U2.6 (DRAIN3)
unnamed: D1008.1 (A), R22.2
unnamed: D1008.2 (K), U3.11 (DRAIN4)
unnamed: D1009.1 (A), R23.2
unnamed: D1009.2 (K), U3.12 (DRAIN5)
unnamed: D1010.1 (A), R24.2
unnamed: D1010.2 (K), U3.13 (DRAIN6)
unnamed: D1011.1 (A), R25.2
unnamed: D1011.2 (K), U3.14 (DRAIN7)
unnamed: D1012.1 (A), R11.2
unnamed: D1012.2 (K), U2.5 (DRAIN2)
unnamed: D1013.1 (A), R10.2
unnamed: D1013.2 (K), U2.4 (DRAIN1)
unnamed: D1014.1 (A), R5.2
unnamed: D1014.2 (K), U2.3 (DRAIN0)
unnamed: D1015.1 (A), R21.2
unnamed: D1015.2 (K), U3.6 (DRAIN3)
unnamed: D1016.1 (A), R20.2
unnamed: D1016.2 (K), U3.5 (DRAIN2)
unnamed: D1017.1 (A), R19.2
unnamed: D1017.2 (K), U3.4 (DRAIN1)
unnamed: D1018.1 (A), R18.2
unnamed: D1018.2 (K), U3.3 (DRAIN0)
unnamed: J2.2, U1.2 (GPIO1)
unnamed: J2.3, U1.1 (GPIO0)
unnamed: J2.4, U1.41 (SWCLK)
unnamed: J2.5, U1.42 (GND)
unnamed: J2.6, U1.43 (SWDIO)
unnamed: Q1.1 (G), R1.2, R2.1
unnamed: R3.2, U2.7 (~CLR)
unnamed: R6.2, SW1.1 (A), SW2.1 (A), SW3.1 (A), SW4.1 (A)
unnamed: R7.2, SW5.1 (A), SW6.1 (A), SW7.1 (A), SW8.1 (A)
unnamed: R8.2, SW9.1 (A), SW10.1 (A), SW11.1 (A), SW12.1 (A)
unnamed: R9.2, SW13.1 (A), SW14.1 (A)
unnamed: R17.2, U3.7 (~CLR)
unnamed: R26.2, U4.7 (~CLR)
unnamed: R29.1, U5.8 (OE)
unnamed: U2.9 (SER/OUT), U3.2 (SER/IN)
unnamed: U3.9 (SER/OUT), U4.2 (SER/IN)

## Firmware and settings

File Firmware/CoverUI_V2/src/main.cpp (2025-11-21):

#include <Arduino.h>
#include <Automaton.h>
#include <PacketSerial.h>
#include <FastCRC.h>
#include "shiftregister/ShiftRegister.h"
#include "DummyOut.h"
#include "pinDefinitions.h"
#include "Atm_button_matrix.h"
#include "Atm_virtual_led.hpp"
#include <bitset>
#include "BttnCtl.h"

#define BM_OUT_SA1 p15
#define BM_OUT_SA2 p16
#define BM_OUT_SA3 p17
#define BM_OUT_SA4 p18

#define BM_IN_SE1 p19
#define BM_IN_SE2 p20
#define BM_IN_SE3 p21
#define BM_IN_SE4 p22

#define BUZZER_OUT p26

#define UNUSED_PIN p14

mbed::DigitalOut PIN_RCK = mbed::DigitalOut(p11);
mbed::DigitalOut PIN_SER = mbed::DigitalOut(p12);
mbed::DigitalOut PIN_SRCK = mbed::DigitalOut(p10);
mbed::DigitalOut PIN_G = mbed::DigitalOut(p13);
mbed::DigitalOut no_pin = DummyOut(UNUSED_PIN);

ShiftRegister shiftRegister = ShiftRegister(
        PIN_SRCK,
        PIN_SER,
        PIN_RCK,
        no_pin,
        PIN_G
);

std::bitset<18> LEDS;

Atm_led builtin_led;
Atm_led buzzer;
Atm_button_matrix SW[14];
Atm_virtual_led leds[18];

// Maps led index to its actual position in chain of shift registers. First bit is furthest in chain
// i.e. Led D0102 is second. It's index is 1, counting from 0
// It mapped to 12th in bit chain from the end (counting from 0)
constexpr byte LED_INDEX_TO_BIT_POSITION[] = {1, 12, 11, 10, 0, 13, 14, 5, 4,
                                              3, 2, 15, 16, 17, 6, 7, 8, 9};

#define FIRMWARE_VERSION 200
FastCRC16 CRC16;
PacketSerial_<COBS, 0, 1024> myPacketSerial;
UART Serial2(p4, p5);

void virtualLedCallback(int idx, int isPressed, int _ignored) {
    LEDS.set(LED_INDEX_TO_BIT_POSITION[idx], isPressed);
    shiftRegister.write(LEDS.to_ulong(), LEDS.size());

#ifdef DEBUG
    Serial.print("LED ");
    Serial.print(idx);
    Serial.print("\t");
    Serial.println(LEDS.to_ulong(), BIN);
#endif
};

void parseLedsBinaryStatus(std::bitset<LEDS.size() * 3> ledsMessage) {
    for (size_t i = 0; i < LEDS.size(); ++i) {

#ifdef DEBUG
        Serial.print(i);
        Serial.print(ledsMessage[i * 3]);
        Serial.print(ledsMessage[i * 3 + 1]);
        Serial.println(ledsMessage[i * 3 + 2]);
#endif
        // LED order is reversed
        auto mapped_led_index = LEDS.size() - 1 - i;
        if (ledsMessage[i * 3 + 2] == 0) {
            leds[mapped_led_index].off();
        } else if (ledsMessage[i * 3 + 1] == 0) {
            leds[mapped_led_index].blink(200, 1000).start();       // Slow
        } else if (ledsMessage[i * 3] == 0) {
            leds[mapped_led_index].blink(200, 200).start();        // Fast
        } else {
            leds[mapped_led_index].on();
        }
    }
}


/****************************************************************************************************
 * sendMessage send the command structure via COBS and serial Port
 *****************************************************************************************************/
void sendMessage(uint8_t *message, size_t size) {
    // packages need to be at least 1 byte of type, 1 byte of data and 2 bytes of CRC
    if (size < 4) {
        return;
    }

    // calculate the CRC
    auto *crc_pointer = (uint16_t *) (message + (size - 2));
    *crc_pointer = CRC16.ccitt(message, size - 2);

#ifdef DEBUG
    // structure is filled and CRC calculated, so print out, what should be encoded
    printf("\nprint struct before encoding %d byte : ", (int) size);
    uint8_t *temp = message;
    for (int i = 0; i < size; i++) {
        printf("0x%02x , ", *temp);
        temp++;
    }
#endif

    myPacketSerial.send(message, size);
}

void reportButtonPress(int idx, int duration) {
    // Mild debug to show that we sense button presses
    builtin_led.toggle();

    struct msg_event_button reply{};
    reply.type = Get_Button;
    // Button ids are 1-indexed
    reply.button_id = idx + 1;
    // ROS expects 0 = single, 1 = long, 2 = very long
    reply.press_duration = duration - 1;

    Serial.print("BTN ");
    Serial.print(reply.button_id);
    Serial.print(" length ");
    Serial.println(reply.press_duration);

    sendMessage((uint8_t *) &reply, sizeof(reply));
}

// When an encoded packet is received and decoded, it will be delivered here.
// The `decoded_buffer` is a pointer to the decoded byte array. `data_size` is the number of
// bytes in the `buffer`.
void onPacketReceived(const uint8_t *decoded_buffer, size_t data_size) {
    // calculate the CRC only if we have at least three bytes (two CRC, one data)
    if (data_size < 3)
        return;

    auto calc_crc = CRC16.ccitt(decoded_buffer, data_size - 2);
    auto bad_crc = false;

    if (decoded_buffer[0] == Get_Version && data_size == sizeof(struct msg_get_version)) {
        Serial.println("Get_Version");
        auto message = (struct msg_get_version *) decoded_buffer;
        if (message->crc == calc_crc) {
            // valid get_version request, send reply
            struct msg_get_version reply{};
            reply.type = Get_Version;
            reply.version = FIRMWARE_VERSION;
            sendMessage((uint8_t *) &reply, sizeof(reply));
        } else
            bad_crc = true;
    } else if (decoded_buffer[0] == Set_Buzzer && data_size == sizeof(struct msg_set_buzzer)) {
        auto message = (struct msg_set_buzzer *) decoded_buffer;
        if (message->crc == calc_crc) {
            Serial.println("Set_Buzzer");
            buzzer.blink(message->on_time, message->off_time, message->repeat).start();
        } else
            bad_crc = true;
    } else if (decoded_buffer[0] == Set_LEDs && data_size == sizeof(struct msg_set_leds)) {
        auto message = (struct msg_set_leds *) decoded_buffer;
        if (message->crc == calc_crc) {
            Serial.println("Set_Leds");
            parseLedsBinaryStatus(std::bitset<LEDS.size() * 3>(message->leds));
        } else
            bad_crc = true;

    } else {
        Serial.println("Invalid command code");
    }

    if (bad_crc)
        Serial.println("Invalid CRC");
}

void setup() {
    LEDS.reset();
    shiftRegister.write(LEDS.to_ulong(), LEDS.size());

    // Setting huge debounce to mitigate potential FIFO spamming with button presses
    SW[0].begin(BM_OUT_SA1, BM_IN_SE1).debounce(50).longPress(3, 300);
    SW[1].begin(BM_OUT_SA1, BM_IN_SE2).debounce(50).longPress(3, 300);
    SW[2].begin(BM_OUT_SA1, BM_IN_SE3).debounce(50).longPress(3, 300);
    SW[3].begin(BM_OUT_SA1, BM_IN_SE4).debounce(50).longPress(3, 300);
    SW[4].begin(BM_OUT_SA2, BM_IN_SE1).debounce(50).longPress(3, 300);
    SW[5].begin(BM_OUT_SA2, BM_IN_SE2).debounce(50).longPress(3, 300);
    SW[6].begin(BM_OUT_SA2, BM_IN_SE3).debounce(50).longPress(3, 300);
    SW[7].begin(BM_OUT_SA2, BM_IN_SE4).debounce(50).longPress(3, 300);
    SW[8].begin(BM_OUT_SA3, BM_IN_SE1).debounce(50).longPress(3, 300);
    SW[9].begin(BM_OUT_SA3, BM_IN_SE2).debounce(50).longPress(3, 300);
    SW[10].begin(BM_OUT_SA3, BM_IN_SE3).debounce(50).longPress(3, 300);
    SW[11].begin(BM_OUT_SA3, BM_IN_SE4).debounce(50).longPress(3, 300);
    SW[12].begin(BM_OUT_SA4, BM_IN_SE1).debounce(50).longPress(3, 300);
    SW[13].begin(BM_OUT_SA4, BM_IN_SE2).debounce(50).longPress(3, 300);

    buzzer.begin(BUZZER_OUT);
    builtin_led.begin(LED_BUILTIN);
    for (size_t i = 0; i < LEDS.size(); ++i) {
        leds[i].begin();

        // Virtual led on/off codes does nothing, instead we update shift register bytes in callback
        leds[i].onEventOn(virtualLedCallback, i);
        leds[i].onEventOff(virtualLedCallback, i);
    }

#ifndef TEST_MODE
    for (int i = 0; i < 14; ++i) {
        SW[i].onPress([](int idx, int v, int up) {
            // v is 0 for release, 1-2-3 for press length
            if (v > 0)
                reportButtonPress(idx, v);
        }, i);
    }
#endif

    Serial2.begin(115200);
    myPacketSerial.setStream(&Serial2);
    myPacketSerial.setPacketHandler(&onPacketReceived);

#ifdef TEST_MODE
    buzzer.blink(200, 5000).start();        // Once in 5s not to irritate people much

    for (size_t i = 0; i < LEDS.size(); ++i) {
        leds[i].begin().blink(50 * (i + 1), 50 * (i + 1)).start();
    };
    for (int i = 0; i < 13; ++i) {
        // Switches SW1-SW13 toggle corresponding leds
        SW[i].onPress([](int idx, int v, int up) {
            Serial.print("TEST BTN ");
            Serial.println(idx);
            builtin_led.toggle();
            leds[idx].toggle();
        }, i).trace(Serial);
    }
    // Switch SW14 operates the rest of leds
    SW[13].onPress([](int idx, int v, int up) {
        if(v == 3) {
            Serial.print("BTN ");
            Serial.println(idx);
            builtin_led.toggle();
            leds[13].toggle();
            leds[14].toggle();
            leds[15].toggle();
            leds[16].toggle();
            leds[17].toggle();
        }
    }, 13).trace(Serial);
#endif

}

void loop() {
    automaton.run();
    myPacketSerial.update();

    // Check for a receive buffer overflow (optional).
    if (myPacketSerial.overflow()) {
        // Send an alert via a pin (e.g. make an overflow LED) or return a
        // user-defined packet to the sender.
        Serial.println("Overflow!");
    }
}

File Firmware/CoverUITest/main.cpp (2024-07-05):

/**
 *  Version 0.93 v. 10.11.2023  AH: Add subscribe packet, change --lcd option functionality
 *  Version 0.92 v. 15.09.2023  AH: Switch to getopt and add --lcd option
 *  Version 0.91 v. 27.05.2022  CE: schnelles Blinken von ontime 500 auf 250 ms verkleinert
 */

// #define _serial_debug_
// #define _testCOBS_

#include <stdio.h>
#include <string>
#include <cstdlib>
#include <cstring>
#include <stdexcept>
#include <iostream>
#include <exception>

#include <chrono>
#include <thread>

// Linux headers
#include <fcntl.h>   // Contains file controls like O_RDWR
#include <errno.h>   // Error integer and strerror() function
#include <termios.h> // Contains POSIX terminal control definitions
#include <unistd.h>  // write(), read(), close()
#include <getopt.h>  // GNU getopt to parse command-line options

#include "COBS.h"
#include "BttnCtl.h"
#include "datatypes.h"
#include "CRC.h"
#include <cmath>
using namespace std;

COBS cobs;
#define buffersize 256

/* --- PRINTF_BYTE_TO_BINARY macro's --- */
#define PRINTF_BINARY_PATTERN_INT8 "%c%c%c%c%c%c%c%c"
#define PRINTF_BYTE_TO_BINARY_INT8(i) (((i) & 0x80ll) ? '1' : '0'), (((i) & 0x40ll) ? '1' : '0'), (((i) & 0x20ll) ? '1' : '0'), (((i) & 0x10ll) ? '1' : '0'), \
                                      (((i) & 0x08ll) ? '1' : '0'), (((i) & 0x04ll) ? '1' : '0'), (((i) & 0x02ll) ? '1' : '0'), (((i) & 0x01ll) ? '1' : '0')
/* --- end PRINTF_BYTE_TO_BINARY macros --- */

#define BATT_ABS_MAX 28.7f
#define BATT_ABS_Min 21.7f

#define BATT_FULL BATT_ABS_MAX - 0.3f
#define BATT_EMPTY BATT_ABS_Min + 0.3f

static string VERSION = "V 0.92";
char DEFAULT_SERIAL[] = "/dev/ttyUSB0";

static uint number_inbuffer = 0;
uint8_t read_buf[buffersize];
uint8_t serial_buf[buffersize];
uint32_t read_ptr = 0;
uint32_t write_ptr = 0;
uint8_t COBS_buf[buffersize];

uint bar_test_delay = 20;
struct ll_status status_message = {0};                  // LL state
struct ll_high_level_state last_high_level_state = {0}; // HL state
uint8_t ui_topic_bitmask = Topic_set_leds;              // UI subscription, default to Set_LEDs
uint16_t ui_interval = 1000;                            // UI send msg (LED/State) interval (ms)

/****************************************************************************************************
 *
 * PacketReceived() there is a serial stream in the buffer
 * decode it with cobs, calc crc and decode into the messagestruct
 *****************************************************************************************************/

void PacketReceived()
{
#ifdef _serial_debug_
    printf("\nPacketReceived()");
    printf("\nbefore decode count = %d values are ", number_inbuffer);
    for (int i = 0; i < number_inbuffer; i++)
    {
        printf(", 0x%02x", COBS_buf[i]);
    }
#endif

    // deocode COBS
    uint8_t decoded_buffer[number_inbuffer];
    size_t data_size = cobs.decode(COBS_buf, number_inbuffer - 1, (uint8_t *)decoded_buffer);

#ifdef _serial_debug_
    printf("\nafter decode count = %d values are ", (int)data_size);
    for (int i = 0; i < data_size; i++)
    {
        printf(", 0x%02x", decoded_buffer[i]);
    }
#endif

    // calculate the CRC
    if (data_size < 3)
        return;
    uint16_t calc_crc = CRC::Calculate(decoded_buffer, data_size - 2, CRC::CRC_16_CCITTFALSE());

    if (decoded_buffer[0] == Get_Version && data_size == sizeof(struct msg_get_version))
    {
        struct msg_get_version *message = (struct msg_get_version *)decoded_buffer;
        if (message->crc == calc_crc)
        {
            printf("button board has version: %d\n", message->version);
        }
        else
        {
            printf("GetVersion invalid CRC");
        }
    }
    else if (decoded_buffer[0] == Get_Button && data_size == sizeof(struct msg_event_button))
    {
        struct msg_event_button *message = (struct msg_event_button *)decoded_buffer;
        if (message->crc == calc_crc)
        {
            printf("button %d was pressed with duration %d\n", message->button_id, message->press_duration);
        }
        else
        {
            printf("Get_Button invalid CRC");
        }
    }
    else if (decoded_buffer[0] == Get_Rain && data_size == sizeof(struct msg_event_rain))
    {
        struct msg_event_rain *message = (struct msg_event_rain *)decoded_buffer;
        if (message->crc == calc_crc)
        {
            printf("rain value %d (threshold %d)\n", message->value, message->threshold);
        }
        else
        {
            printf("Get_Rain invalid CRC");
        }
    }
    else if (decoded_buffer[0] == Get_Emergency && data_size == sizeof(struct msg_event_emergency))
    {
        struct msg_event_emergency *message = (struct msg_event_emergency *)decoded_buffer;
        if (message->crc == calc_crc)
        {
            printf("Emergency state " PRINTF_BINARY_PATTERN_INT8 "\n", PRINTF_BYTE_TO_BINARY_INT8(message->state));
        }
        else
        {
            printf("Get_Emergency invalid CRC");
        }
    }
    else if (decoded_buffer[0] == Get_Subscribe && data_size == sizeof(struct msg_event_subscribe))
    {
        struct msg_event_subscribe *message = (struct msg_event_subscribe *)decoded_buffer;
        if (message->crc == calc_crc)
        {
            printf("Subscribe to topic_bitmask " PRINTF_BINARY_PATTERN_INT8 ", interval %dms\n", PRINTF_BYTE_TO_BINARY_INT8(message->topic_bitmask), message->interval);
            ui_topic_bitmask = message->topic_bitmask;
            ui_interval = message->interval;
        }
        else
        {
            printf("Get_Subscribe invalid CRC");
        }
    }
}

/****************************************************************************************************
 *
 * reply wait for timeout ms if return with result
 *
 *****************************************************************************************************/

#define timeout 100

void reply(int com_port)
{
    number_inbuffer = 0;
    std::this_thread::sleep_for(std::chrono::milliseconds(timeout));
    int num_bytes = 0;
    try
    {
        num_bytes = read(com_port, &read_buf, sizeof(read_buf));
    }
    catch (...)
    {
        std::cout << "Serial error check cable " << '\n';
        return;
    }

    //  printf("*** Error *** no connection to target, check cable");

    if (num_bytes != 0)
    {
        for (int i = 0; i < num_bytes; i++)
        {
            serial_buf[write_ptr] = read_buf[i];
            write_ptr++;
            if (write_ptr >= buffersize)
                write_ptr = 0;
        }

#ifdef _serial_debug_

#endif

        while (write_ptr != read_ptr)
        {
            COBS_buf[number_inbuffer] = serial_buf[read_ptr];
            number_inbuffer++;
            read_ptr++;
            if (read_ptr >= buffersize)
                read_ptr = 0;
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

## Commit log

2023-04-20 Initial version
    [stlink.cfg]
2023-04-21 Align LED IDs
2023-04-21 Align LED order to LowLevel code
2023-04-23 Correct LED_NUM_x defines
2023-04-24 Restructure timer, INT priorities, Animation, add LED sequences
2023-04-26 Add debug probe infos
2023-04-27 feat: cover UI HW 1.1.0
    [CoverUI.kicad_pcb, FIX-LEDS-4.5.step]
2023-04-27 chore: rename to Hardware
    [CoverUI.kicad_pcb, CoverUI.kicad_sch, FIX-LEDS-4.5.step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]
2023-04-30 LEDs & Timer work. GD32 partly
2023-04-30 Start Button support
2023-05-01 Eval STM32 bootup issue
2023-05-01 STM32 Timer (prep. for GD32), Picoprobe, cleanup
    [picoprobe.cfg]
2023-05-02 Done HW-Serial, but Arudino Implementation is slow and miss UART ISR
2023-05-04 Finish LEDs, Timer & HardwareSerial
    [picoprobe-gd.cfg, picoprobe-stm.cfg, stlink-gd.cfg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]
2023-05-06 Finish buttons for STM32
2023-05-06 Switch GD32 timer to general purpose timer
2023-05-07 Finish GD32 button support
2023-05-09 Rain & Hall functional & generic rain measurements
2023-05-11 Cleanup & firmware/MOD syntax
    [picoprobe-gd.cfg]
2023-05-23 Stock rain sensor workings well in practice
2023-06-15 Fix typo & add/correct some LED/Button usage infos
2023-08-15 YFC500B Schematics
    [btn.kicad_sch, btns-leds.kicad_sch, led.kicad_sch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]
2023-09-01 First tests & schematics
    [YF-SA600H.kicad_sch, btn.kicad_sch, btns-leds.kicad_sch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]
2023-09-01 Reorganized schematics
    [Classic_500B.kicad_sch, btn.kicad_sch, c500_btns-leds.kicad_sch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]
2023-09-01 Add buttons
    [SAxPRO DotMatrix LCD.kicad_sch, btn.kicad_sch, lcd.kicad_sch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]
2023-09-01 Rename yfc500 folder to more common YardForce
    [picoprobe-stm.cfg, stlink-gd.cfg, stlink-stm.cfg]
2023-09-10 Fix: Actually Register SW14 for button press events
    SW14 has never been registered for button press events. The loop ignores it, because it's missing the last iteration.
    This was most likely a copy & paste mistake from the TEST_MODE code below where SW14 is handled specially and not by a loop iterating over all buttons.
    [main.cpp]
2023-09-11 Restructure into LedSymbol & Bar widgets
2023-09-12 Fix wrong inverse color handling
    [UC1698.cpp]
2023-09-12 Switch to low-priority hardware-timer based lv_timer_handler()
2023-09-13 Add touch panel
    [SAxPRO (DotMatrix LCD).kicad_sch, saxpro_lcd.kicad_sch, saxpro_mcu_stm32f030.kicad_sch]
2023-09-13 Add flash and some cleanup
    [SAxPRO (DotMatrix LCD).kicad_sch, saxpro_btn.kicad_sch, saxpro_mcu_stm32f030.kicad_sch]
2023-09-14 Switch to getopt and add --lcd option
2023-09-15 Finish LED state conversions
2023-09-15 Cosmetic schematic changes
    [SAxPRO (DotMatrix LCD).kicad_sch, saxpro_mcu_stm32f030.kicad_sch]
2023-09-16 Minor LED-2-Symbol adaptions
2023-09-16 Fix and clean debouncer
    [Buttons.hpp]
2023-09-22 Major state handling. Fix backlight timeout malfunction
    [LEDcontrol.cpp]
2023-09-24 Adapt charge bar
2023-09-27 Add volume up, down and language switch
2024-07-05 SA600/900 (RM-ECOW-V1.1.0) support (#10)
    * Add schematics
    * Original FW backup
    * LEDcontrol base- & sub-class separation for RM-ECOW-V100
    * Nifty restructuration
    * Restructured Button code
    * Reimplemented magic buttons and finished button & LED restructuration
    * Split up Hardware Mods and added RM-ECOW-V1.0.0
    * Evaluated Hall Support
    * Evaluated Hall Support
    * Fixed links
    * Started backport of C500- STM32 & GD32. Broken!
    * Finished backport of C500- STM & GD32
    * Passed by reference instead value
    * Adapted Emergency for common C500 & RMECOWV100 usage
    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
    [NX100i 18Button-3LED-LCD Board.kicad_sch, SA,SC-Type 10Button-12LED Board.kicad_sch, SA650 9Button-11LED Board.kicad_sch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]
2024-10-03 Support for SA900 CoverUI with STM32 MCU and ... (#11)
    * Add RM-ECOW-V1.1.0 STM32 support
    * Remove Picoprobe support
    * Add new variant to CI
    * Add MOD_HALL to RM-ECOW-V1.0.0
    * Restructure docs and add HALL support to RM-ECOW-V1.0.0
    * Fix heap overflow
    * Some minor adaptions
    * Refactor stock YF part
    * Fix missing artifact
    * Fix missing artifact
    [SA,SC-Type 10Button-12LED Board.kicad_sch, btn.kicad_sch, btns-leds.kicad_sch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]

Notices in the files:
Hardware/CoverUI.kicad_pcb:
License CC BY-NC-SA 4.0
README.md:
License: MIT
